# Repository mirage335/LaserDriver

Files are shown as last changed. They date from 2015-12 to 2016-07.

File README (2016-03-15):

Copyright (C) 2015 mirage335
See the end of the file for license conditions.
See license.txt for LaserDriver license conditions.

#Usage
Variable power laser driver, usable with diodes like NBD7878 and BDR-209, on machines like the Taz_Mega and LulzBot Taz. Takes <24V ~30kHz PWM control signal, 12V power, and drives laser at 2W-3W maximum optical power.

#Design
Basic voltage controlled current source. Common collector transistor amplifier attempts to maintain given voltage across emitter resistor. Consequently, the collector load (ie. laser) is allowed to source just enough current to maintain that voltage.

Low-value collector load is placed behind a safety switch. Optical output with this switch open is expected to be <<100mW, likely <2mW.

#Extras
Lockout and InterfaceBuffered PCBs are not required. Lockout PCB may be used to delay startup, which should not be necessary. InterfaceBuffered adds an OpAmp for better regulation, which is also not necessary, and slightly reduces stability margins.

#Pinouts
From PatchRap.

##Laser
	3 / 1 - 5V
	3 \ 2 - sGND
	2 - 3 - Vsys
	1 / 4 - 12V (Must be powered internally or externally.)
	1 \ 5 - pGND
	2 - 6 - pGND
	4 / 7 - PWM (Digital Control)
	4 \ 8 - sGND

###Drive
Laser drive electronic designs may wish to follow similar standards.
####Tool
	3 / 1 - 5V
	3 \ 2 - sGND
	2 - 3 - PWR+ (Laser)
	1 / 4 - 12V
	1 \ 5 - pGND
	2 - 6 - PWR- (Laser)
	4 / 7 - PWR+ (Laser)
	4 \ 8 - PWR- (Laser)

####Interface
	3 / 1 - 5V
	3 \ 2 - sGND
	2 - 3 - Emitter (Enable, Ammeter)
	1 / 4 - 12V
	1 \ 5 - pGND
	2 - 6 - pGND
	4 / 7 - PWM (Digital Control)
	4 \ 8 - Sig (Analog Control)

#Binary Mode
Potentiometers are provided for configuration down to extremely low-power (<<3mW) maximum output, in addition to a "binary" bypass switch. For photolithography, this allows the laser to be rapidly switched on at a precise power level, calibrated to expose the photoresist. Vector writing recommended, or at least vector then raster.

#Future Work
*) Switching power supply using similar pinout. Chips to consider include the LT3518, LED5000, TPS92513HV, LM3409HV, and others.
*) Programmable ultra-fast (<<200ns) pulse-mode laser driver using similar pinout.
*) Beam stearing optoelectronics, for VLSI photolithographic exposure image projection.

#Safety
Big scary laser. Do not examine with remaining eye. Seriously.

High-power, Class 4 near-UV lasers, such as BDR-209 and NDB7875 are extraordinarily hazardous. Backscatter from the projected spot alone is sufficient to slice a retina. Avoid exposure, and wear eye protection.

Beware common grounding and other issues may falsely trigger the control transistor. In general, the laser system should be consiered dangerous whenever powered, particularly when the "SAFETY" switch is closed.

No claim of liability is made by anyone. Your accident is your accident. Use common sense, and follow all regulations. If you don't understand the safety features and limitations, don't use this circuit or anything similar.

#References
https://www.fairchildsemi.com/datasheets/ti/tip120.pdf
https://sites.google.com/site/dtrlpf/home/diodes/9mm-445nm
https://www.sparkfun.com/datasheets/Prototyping/General/PRT-09576-6400BG.pdf

#Copyright
This file is part of LaserDriver.

LaserDriver is free software: you can redistribute it and/or modify
it under the terms of the GNU General Public License as published by
the Free Software Foundation, either version 3 of the License, or
(at your option) any later version.

LaserDriver is distributed in the hope that it will be useful,
but WITHOUT ANY WARRANTY; without even the implied warranty of
MERCHANTABILITY or FITNESS FOR A PARTICULAR PURPOSE.  See the
GNU General Public License for more details.

You should have received a copy of the GNU General Public License
along with LaserDriver.  If not, see <http://www.gnu.org/licenses/>.

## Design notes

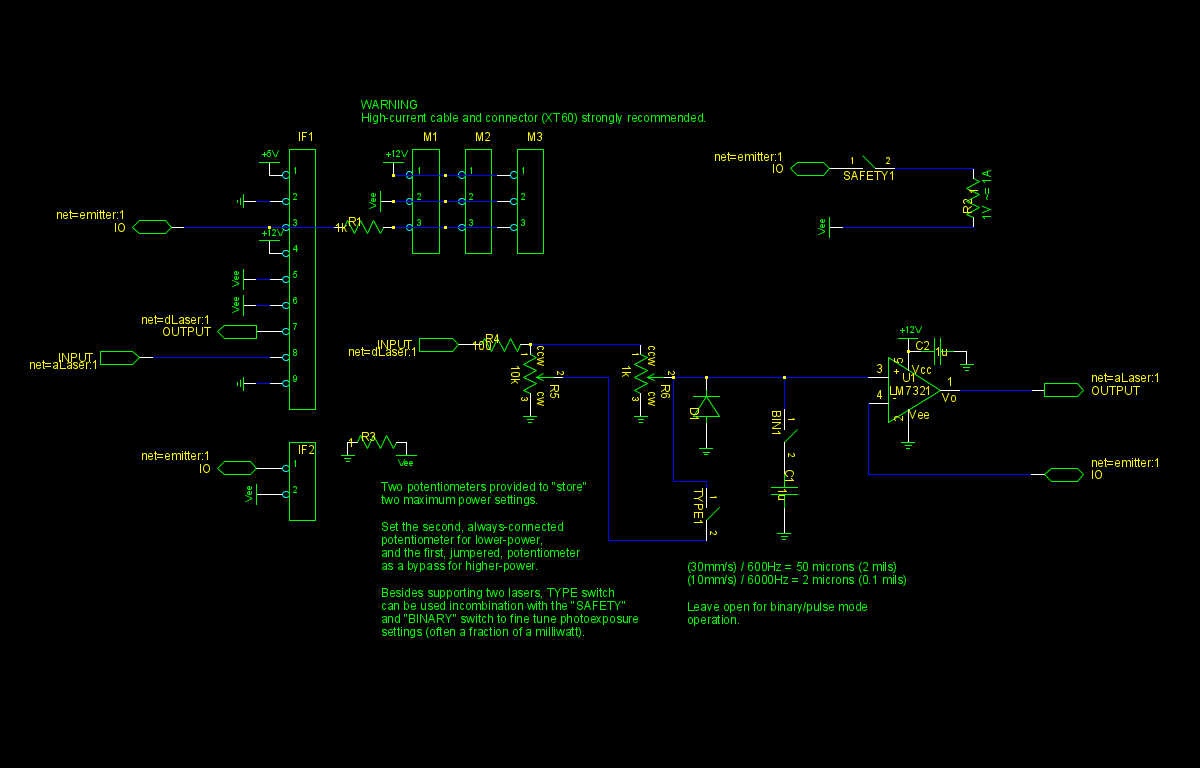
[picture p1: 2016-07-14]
InterfaceBuffered.png

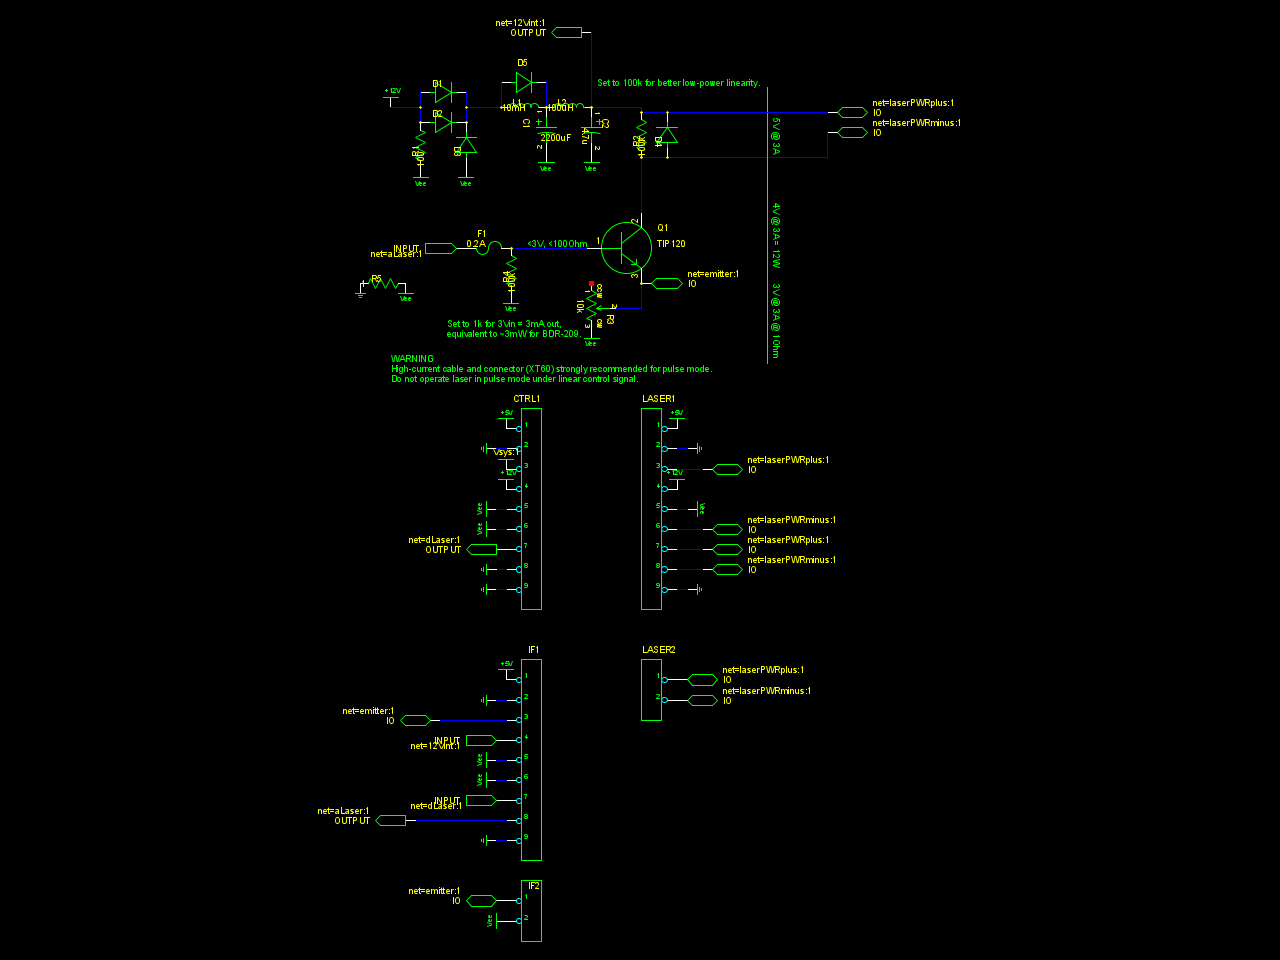
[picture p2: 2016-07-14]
LaserDriver.png

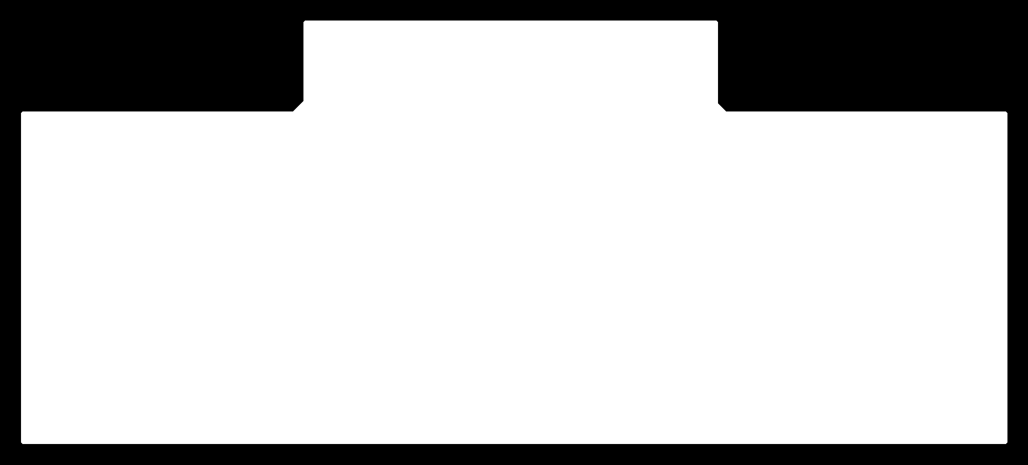
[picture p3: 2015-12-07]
productionStatic/hacdcCNC/Lockout/outp3_outline_filled.png

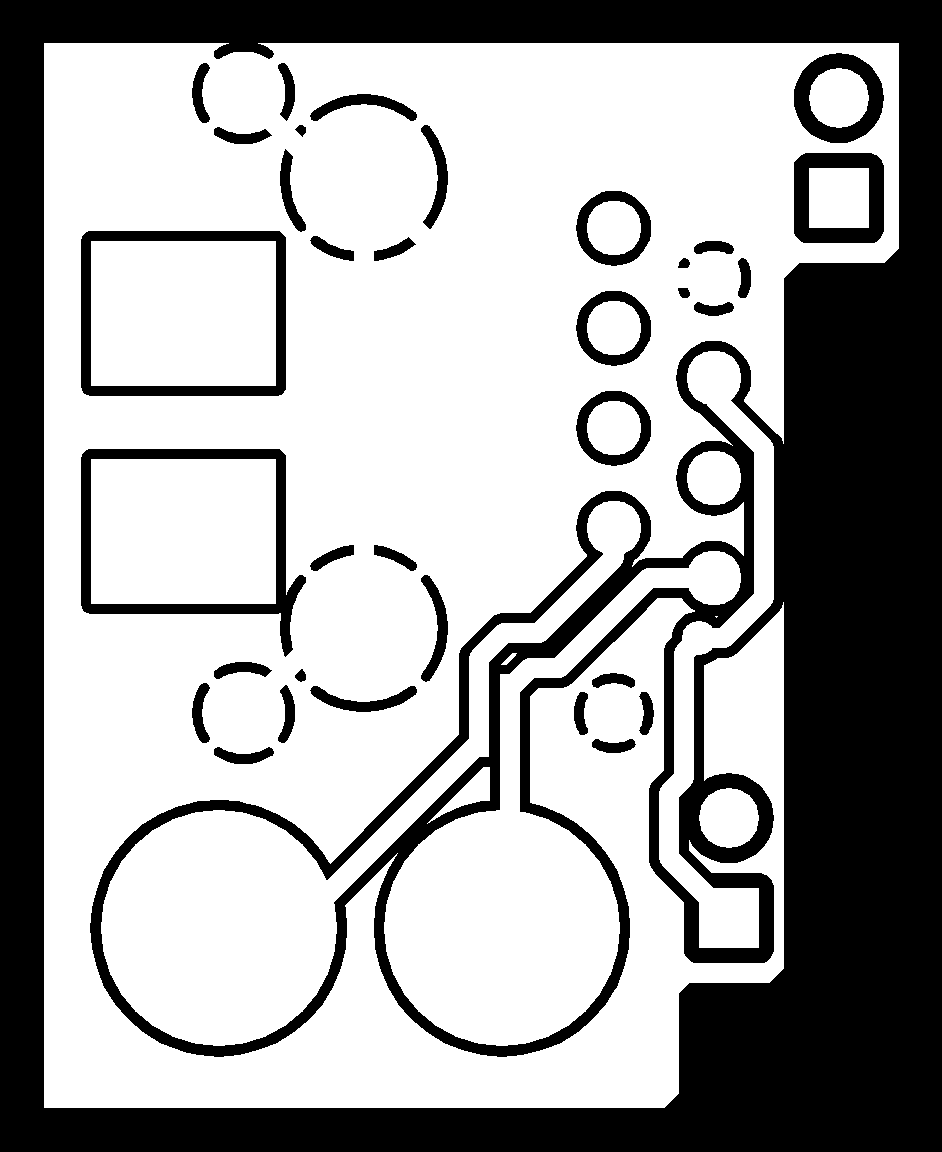
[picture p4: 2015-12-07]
productionStatic/hacdcCNC/Laser/outp0_original_back.png

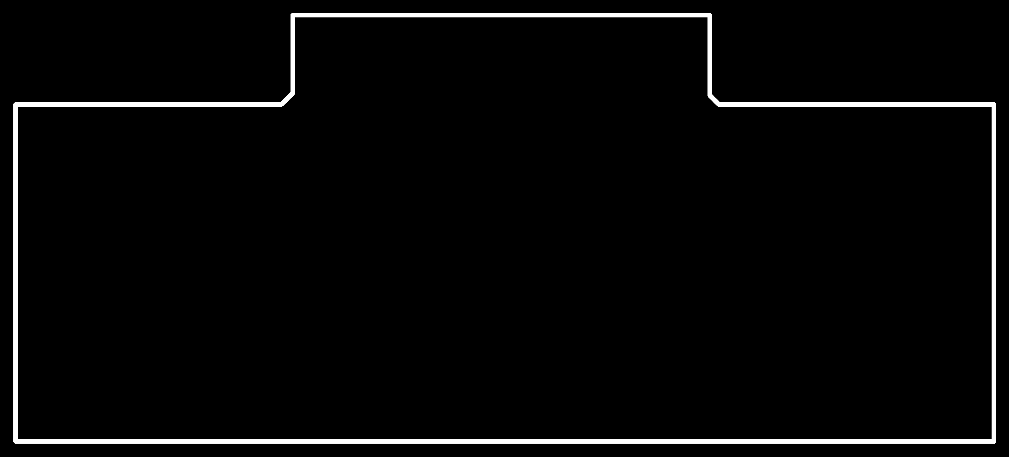
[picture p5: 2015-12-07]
productionStatic/hacdcCNC/Lockout/outp2_original_outline.png

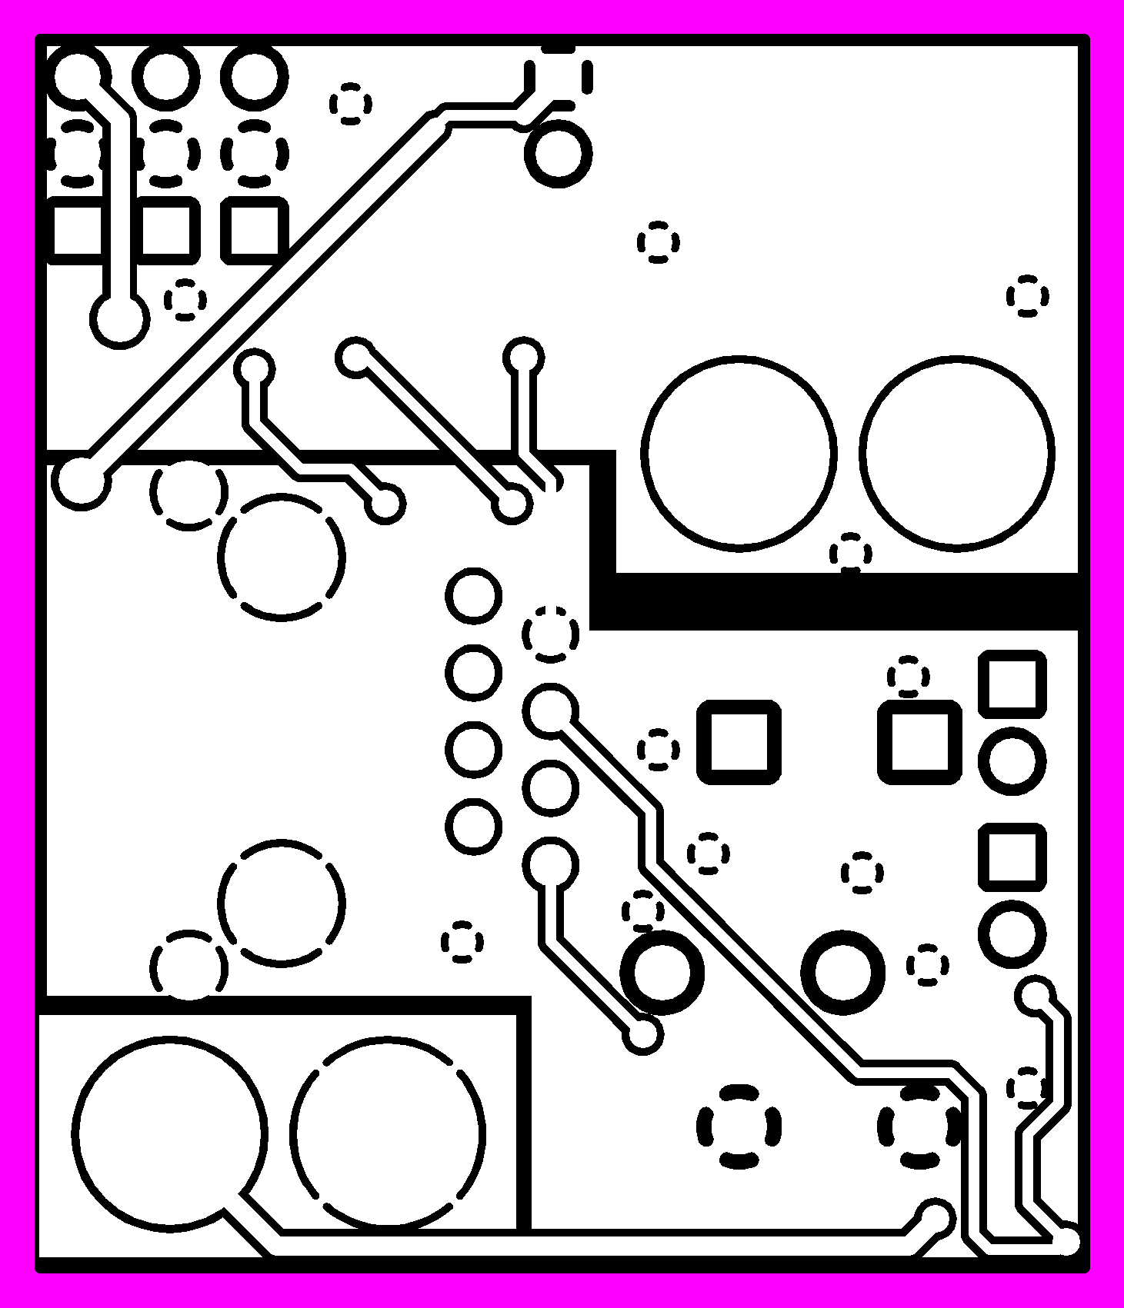
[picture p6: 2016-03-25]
productionStatic/hacdcCNC/InterfaceBuffered/outp4_masked.png

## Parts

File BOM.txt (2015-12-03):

1 * Digital Panel Voltmeter - http://www.adafruit.com/products/705 
1 * Analog Panel Voltmeter - http://www.amazon.com/dp/B00PFBFLB2/?tag=hacdc-20 OR http://www.amazon.com/dp/B00PFBFLB2/?tag=hacdc-20 OR http://www.amazon.com/dp/B009PKEJ44/?tag=hacdc-20NB

2 * XT60 Connectors - http://www.hobbyking.com/hobbyking/store/__9572__Nylon_XT60_Connectors_Male_Female_5_pairs_GENUINE.html

1 * S/FTP Cat6A Cable - http://www.amazon.com/dp/B004NPL4YE/?tag=hacdc-20

1 * Transistor Heatsink - http://www.digikey.com/product-detail/en/6400BG/6400BG-ND/1625171 OR https://www.sparkfun.com/products/9576

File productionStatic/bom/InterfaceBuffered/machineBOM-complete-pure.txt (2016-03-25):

IF1:CONNECTOR_9:-:538-95540-2881:$1.75 MOUSER 538-95540-2881:1
R4:RESISTOR:100:1206:$0.10 MOUSER 71-CRCW1206-100-E3 :1
R6:VARIABLE_RESISTOR:1k:VISHAY_T18:$1.84 MOUSER 72-T18-1K:1
R2:RESISTOR:1:JUMPER2:$1.15 MOUSER 71-RS0051R000FE12 :1
SAFETY1:SPST:60A:XT60:$0.80 HobbyKing XT60:1
D1:DIODE:-:DO214AB:$0.55 MOUSER 512-ES3J:1
R1:RESISTOR:1k:1206:$0.10 MOUSER 71-CRCW1206-1.0K-E3:1
IF2:CONNECTOR_2:60A:XT60:$0.80 HobbyKing XT60:1
M1,M2,M3:CONNECTOR_3:-:JUMPER3:-:3
BIN1,TYPE1:SPST:-:JUMPER2:-:2
R3:RESISTOR:1:0402:$0.10 MOUSER 71-CRCW0402-1-E3:1
R5:VARIABLE_RESISTOR:10k:VISHAY_T18:$2.04 MOUSER 72-T18-10K:1
U1:LM7321:-:SOT23-5:$2.20 MOUSER 926-LM7321MF:1
C1,C2:CAPACITOR:1u:0603:$0.15 MOUSER 80-C0603C105K3P:2

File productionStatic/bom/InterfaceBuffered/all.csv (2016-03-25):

(IF1) | CONNECTOR_9 | - | 538-95540-2881 | $1.75 MOUSER 538-95540-2881 | 1 | $1.75 | 538-95540-2881 | 1
(R4) | RESISTOR | 100 | 1206 | $0.10 MOUSER 71-CRCW1206-100-E3 | 1 | $0.10 | 71-CRCW1206-100-E3 | 1
(R6) | VARIABLE_RESISTOR | 1k | VISHAY_T18 | $1.84 MOUSER 72-T18-1K | 1 | $1.84 | 72-T18-1K | 1
(R2) | RESISTOR | 1 | JUMPER2 | $1.15 MOUSER 71-RS0051R000FE12 | 1 | $1.15 | 71-RS0051R000FE12 | 1
(SAFETY1) | SPST | 60A | XT60 | $0.80 HobbyKing XT60 | 1 | $0.80 |  | 1
(D1) | DIODE | - | DO214AB | $0.55 MOUSER 512-ES3J | 1 | $0.55 | 512-ES3J | 1
(R1) | RESISTOR | 1k | 1206 | $0.10 MOUSER 71-CRCW1206-1.0K-E3 | 1 | $0.10 | 71-CRCW1206-1.0K-E3 | 1
(IF2) | CONNECTOR_2 | 60A | XT60 | $0.80 HobbyKing XT60 | 1 | $0.80 |  | 1
(M1|M2|M3) | CONNECTOR_3 | - | JUMPER3 | - | 3 | - |  | 3
(BIN1|TYPE1) | SPST | - | JUMPER2 | - | 2 | - |  | 2
(R3) | RESISTOR | 1 | 0402 | $0.10 MOUSER 71-CRCW0402-1-E3 | 1 | $0.10 | 71-CRCW0402-1-E3 | 1
(R5) | VARIABLE_RESISTOR | 10k | VISHAY_T18 | $2.04 MOUSER 72-T18-10K | 1 | $2.04 | 72-T18-10K | 1
(U1) | LM7321 | - | SOT23-5 | $2.20 MOUSER 926-LM7321MF | 1 | $2.20 | 926-LM7321MF | 1
(C1|C2) | CAPACITOR | 1u | 0603 | $0.15 MOUSER 80-C0603C105K3P | 2 | $0.15 | 80-C0603C105K3P | 2

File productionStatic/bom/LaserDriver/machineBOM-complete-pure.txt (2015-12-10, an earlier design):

Q1:TIP120:-:TO220:$0.65 MOUSER 512-TIP120:1
CTRL1,IF1,LASER1:CONNECTOR_9:-:538-95540-2881:$1.75 MOUSER 538-95540-2881:3
L1:INDUCTOR:10mH:RADIAL_CAN 400:$1.39 MOUSER 652-RL181S-103J-RC:1
C1:POLARIZED_CAPACITOR:2200uF:RCY300P:$2.04 MOUSER 80-ESH228M050AN2AA:1
C2:POLARIZED_CAPACITOR:4.7u:2917p:$0.64 MOUSER 74-293D475X0050D2TE3:1
L2:INDUCTOR:100uH:1206:$0.90 MOUSER 652-SRR1206-101YL:1
F1:FUSE:0.2A:ACY200:X $0.94 MOUSER 576-600R150-RA:1
R1:RESISTOR:100:JUMPER2:$0.34 MOUSER 71-CP0005100R0JE14 :1
D1,D2,D3,D4:DIODE:-:DO214AB:$0.55 MOUSER 512-ES3J:4
IF2,LASER2:CONNECTOR_2:60A:XT60:$0.80 HobbyKing XT60:2
R3:VARIABLE_RESISTOR:10k:VISHAY_T18:$2.04 MOUSER 72-T18-10K:1
D5:DIODE:3A:Diode_DO-201AD_Horizontal_RM15:$0.32 MOUSER 583-RL851-B:1
R2,R4:RESISTOR:100k:0402:$0.10 MOUSER 71-CRCW0402-100K-E3:2
R5:RESISTOR:1:0402:$0.10 MOUSER 71-CRCW0402-1-E3:1

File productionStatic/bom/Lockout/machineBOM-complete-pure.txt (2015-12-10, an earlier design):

IF1,IF2:CONNECTOR_9:-:538-95540-2881:$1.75 MOUSER 538-95540-2881:2
C1:CAPACITOR:47u:1210:$0.84 MOUSER 80-C1210C476M4P:1
R2:RESISTOR:200:ACY400:$0.07 MOUSER 71-RN60D2260F/R:1
F1:CONNECTOR_2:-:JUMPER2:-:1
R1,R3,R4:RESISTOR:1k:ACY400:$0.10 MOUSER 71-CCF501K00FKE36:3
U1,U2,U3:LCC110:-:DIP8:$4.41 MOUSER 849-LCC110:3
R5:RESISTOR:1:0402:$0.10 MOUSER 71-CRCW0402-1-E3:1

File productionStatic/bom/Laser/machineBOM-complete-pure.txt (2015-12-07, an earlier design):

LASER1:CONNECTOR_9:-:538-95540-2881:$1.75 MOUSER 538-95540-2881:1
L1:LED:-:JUMPER2:-:1
FAN1:CONNECTOR_2:-:JUMPER2:-:1
D1:DIODE:-:DO214AB:$0.55 MOUSER 512-ES3J:1
L2:CONNECTOR_2:60A:XT60:$0.80 HobbyKing XT60:1
C1,C2:CAPACITOR:1n:0402:$0.71 MOUSER 80-C0402C102F5G :2

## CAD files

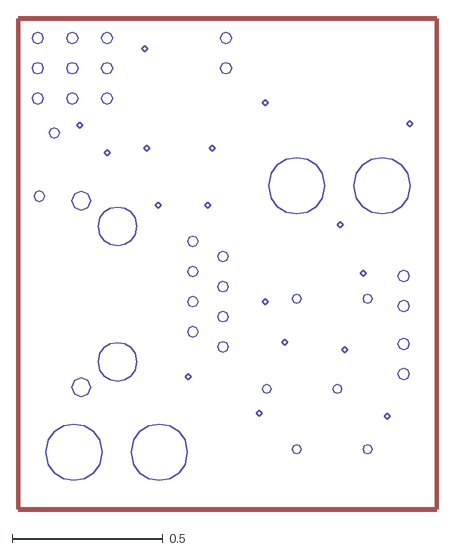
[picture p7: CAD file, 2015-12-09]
productionStatic/cad/Interface/combined.dxf
1.40 x 1.64

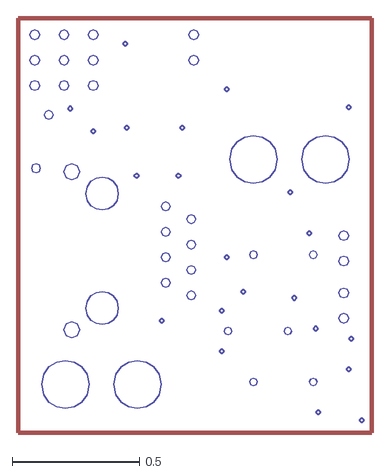
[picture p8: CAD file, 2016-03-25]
productionStatic/cad/InterfaceBuffered/combined.dxf
1.40 x 1.64

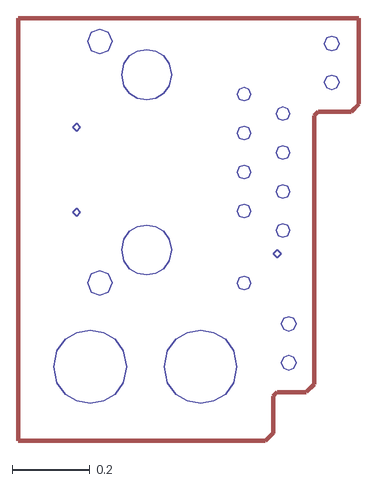
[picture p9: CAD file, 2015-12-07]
productionStatic/cad/Laser/combined.dxf
0.885 x 1.10

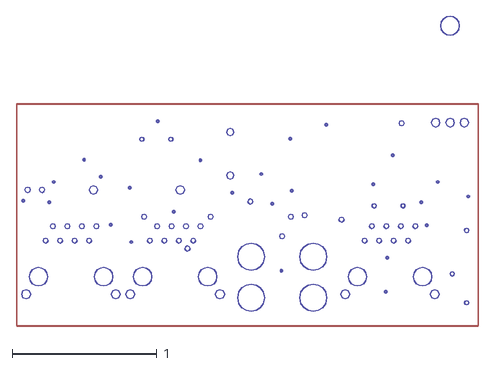
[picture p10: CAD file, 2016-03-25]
productionStatic/cad/LaserDriver/combined.dxf
3.20 x 2.15

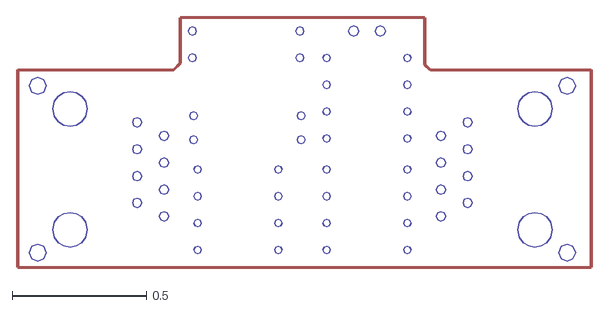
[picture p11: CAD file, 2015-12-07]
productionStatic/cad/Lockout/combined.dxf
2.14 x 0.94

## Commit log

2015-04-16 Basic design.
    [LaserDriver.sch]
2015-04-17 Removed potentially undesirable diodes, corrected 12V GND, updated README.
    [LaserDriver.sch]
2015-04-17 Additional protection diodes.
    [LaserDriver.sch]
2015-04-18 Decoupling capacitors, input load resistor.
    [LaserDriver.sch]
2015-04-20 5VCTRL input.
    [LaserDriver.sch]
2015-11-14 Preparation for compliance with PatchRap.
    [LaserDriver.sch, accessory-sys.sch, laser-sys.sch]
2015-11-15 Pinouts determined, functionality separated.
    [LaserDriver.sch]
2015-11-15 Separate schematics drafted.
    [Interface.sch, Laser.sch, LaserDriver.sch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]
2015-11-15 Laser Driver schematic, accurate footprints and BOM data.
    [LaserDriver.sch]
2015-11-15 Provisions for pulsed mode operation.
    [Interface.sch, Laser.sch, LaserDriver.sch]
2015-11-15 Filter and bias component values adjusted.
    [Interface.sch, Laser.sch, LaserDriver.sch]
2015-11-15 BOM data verified.
    [Interface.sch, Laser.sch, LaserDriver.sch]
2015-11-16 PCB artwork completed.
    [Interface.dsn, Laser.sch]
2015-11-16 Production assets.
    [Interface.bottom.gbr, Interface.bottommask.gbr, Interface.bottompaste.gbr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]
2015-12-03 Cat6A S/FTP cable BOM entry.
2015-12-03 PostScript schematics.
    [LaserDriver.sch]
2015-12-04 Concepts for hybrid laser driver, and soft-start lockout.
    [HybridLaserDriver.sch, Lockout.sch]
2015-12-04 Improved hard start lockout.
    [Lockout.sch]
2015-12-04 Lockout schematic ps file.
    [Lockout.sch]
2015-12-07 Hybrid laser concept dropped, pulse mode support dropped, current regulation margins improved.
    [HybridLaserDriver.sch, Interface.sch, Laser.sch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]
2015-12-07 Updated PCB layouts and production assets.
    [Interface.bottom.gbr, Interface.bottommask.gbr, Interface.bottompaste.gbr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]
2015-12-07 List of possible switching regulators.
2015-12-08 Backup base bias resistor.
    [Interface.bottom.gbr, Interface.bottommask.gbr, Interface.bottompaste.gbr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]
2015-12-09 Internally bond Vee/GND, ensuring interface voltage divider circuitry does not pass unattenuated control signal.
    [Interface.bottom.gbr, Interface.bottommask.gbr, Interface.bottompaste.gbr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]
2015-12-10 Power/signal ground bonding inductor replaced with 1ohm resistor, PWM to analog converter low pass filter capacitor increased to 1uF.
    [Interface.sch, LaserDriver.sch, Lockout.sch]
2015-12-10 Lockout board note.
2016-01-17 BOM info.
    [Interface.bottom.gbr, Interface.bottommask.gbr, Interface.bottompaste.gbr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]
2016-03-15 Some thicker traces, internal 12V supply for interface board, buffered interface schematic.
    [InterfaceBuffered.sch, LaserDriver.sch]
2016-03-15 OpAmp buffered interface PCB.
2016-03-15 OpAmp power supply bypass capacitor, README update.
    [InterfaceBuffered.sch]
